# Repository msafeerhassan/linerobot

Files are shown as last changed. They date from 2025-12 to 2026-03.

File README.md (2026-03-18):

# Line Following Robot with PID
## Project Overview

Line Following Robot with PID project uses IR Sensors, Microcontroller and Motors to follow a line path on the floor. PID is a type of error-reduction algorithm implemented in such robots to reduce their errors and improve accuracy and precision.
## Project Details
This project is built under Hack Club's Blueprint Program. Custom shape PCB is be used as chassis for the car. PCB covers all components routing alongwith components mounting and soldering. This reduces the wires and improve the project's appearance. Moreover, it reduces the weight due to separate chassis making it more efficient.
N20 Gear Motors with encoders and DRV8833 Motor Driver alongwith QTR 8 Channel IR Sensor Array and ESP32 S3 Devkit are being used. Several capacitors are added to improve the current flow. A Lithium Battery powers this whole project. ESP32 is powered by 5V which is regulated via a Buck Convertor. Motors are powered by 6V and this too is regulated through a 6V 5A Buck Converter.

### PCB:





### Schematic Diagram:



### 3D Model Images:





### Why I made this project?

This was my first ever Hardware Project involving Schematic Design and PCB. I chose this project to strengthen my knowledge and skills of using sensors, microcontrollers etc. I learnt a lot about capacitance, optimum current flow and how sensors work inside. This robot will be used to compete in Line Following Robot competitions like: https://www.dmtsnust.com/nerc/. This project, though difficult but still made me believe that I can build efficient and great Hardware Projects too.

### How it will work
Firstly, battery powers everything and voltage is regulated via Buck Convertors. 
Then the IR Sensor Array gives readings to the ESP32 and based on that, ESP32 alters the speed of motors via Motor Driver.
This allows Robot to stay on line.
When PID is implemented, after this step the ESP32 counts error Value and based on that some manual variables are adjusted that results in increased accuracy and precision.
This loop continues until the robot reaches end of line and then it will stop.

### How to use it?

Firstly, order the PCB from PCB Manufacturing Service. I used JLCPCB: http://jlcpcb.com/ because they offer great and high quality services.
Then order all the components listed in the Bill of Materials.
Solder them all onto the PCB and fully assemble it.
Flash the firmware inside the ESP32. Make sure to adjust variables for better results.
BOOM!!! YOU MADE A COOL LINE FOLLOWING ROBOT.

## Bill of Materials (BOM)

| Item Name | Quantity | Link | Cost |
|:---|---:|:---|:---|
| ESP32-DevKit-S3-WROOM1 | 1 | [Link](https://epro.pk/product/pre-soldered-esp32-s3-wroom-1-development-board-2-4g-wifi-bt-module/) | $6.41  |
| DRV8833 Motor Driver | 1 | [Link](https://epro.pk/product/tb6612-drv8833-dual-motor-driver-module-1a-h-bridge-for-arduino-robotics/) | $1.98  |
| 6V N20 Gear Motor with encoder, wheel and mounting brackets | 2 | [Link](https://www.aliexpress.com/item/1005004110888400.html) | $16.35 |
| 5A Buck DC-DC Converter 7.4V to 6V | 1 | [Link](https://www.aliexpress.com/item/4000496873234.html) | $4.84  |
| 7.4V to 5V 1A DC-DC Fixed Buck Convertor (for ESP32) | 1 | [Link](https://www.aliexpress.com/item/1005006005553178.html) | $1.86  |
| 470 µF, 16 V aluminium electrolytic capacitor | 2 | [Link](https://epro.pk/product/470uf-16v-aluminum-electrolytic-capacitor/) | $0.11  |
| 220 µF, 10 V aluminium electrolytic capacitor | 1 | We'll buy it ourself | $0.00  |
| 100 nF Ceramic Capacitor | 2 | [Link](https://epro.pk/product/0-1uf-100nf-100000pf-104-ceramic-capacitor-in-pakistan/) | $0.02  |
| 8 Channel IR Sensor Array | 1 | [Link](https://epro.pk/product/qtr-8rc-line-following-reflectance-ir-sensor-8-channel-line-following-line-tracking-array-module/) | $2.30  |
| LiPo Battery 7.4V 1500mAH | 1 | [Link](https://epro.pk/product/zop-power-7-4v-1500mah-li-po-rechargeable-battery-pack/) | $10.04 |
| PCB | 1 | No Link:( | $36.25 |
| Push Switch Button | 1 | [Link](https://epro.pk/product/slider-on-off-switch/) | $0.05  |
| TAXES:( | 0 | No Link:( | $16.14 |
| Total Cost | 0 | | $96.35 |

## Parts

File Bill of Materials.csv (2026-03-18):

Item Name | Quantity | Sourcing Link | Cost
ESP32-DevKit-S3-WROOM1 | 1 | https://epro.pk/product/pre-soldered-esp32-s3-wroom-1-development-board-2-4g-wifi-bt-module/ | $6.41
DRV8833 Motor Driver | 1 | https://epro.pk/product/tb6612-drv8833-dual-motor-driver-module-1a-h-bridge-for-arduino-robotics/ | $1.98
6V N20 Gear Motor with encoder, wheel and mounting brackets | 2 | https://www.aliexpress.com/item/1005004110888400.html | $16.35
5A Buck DC-DC Converter 7.4V to 6V | 1 | https://www.aliexpress.com/item/4000496873234.html | $4.84
7.4V to 5V 1A DC-DC Fixed Buck Convertor (for ESP32) | 1 | https://www.aliexpress.com/item/1005006005553178.html | $1.86
470 µF, 16 V aluminium electrolytic capacitor | 2 | https://epro.pk/product/470uf-16v-aluminum-electrolytic-capacitor/ | $0.11
220 µF, 10 V aluminium electrolytic capacitor | 1 | We'll buy it ourself | $0.00
100 nF Ceramic Capacitor | 2 | https://epro.pk/product/0-1uf-100nf-100000pf-104-ceramic-capacitor-in-pakistan/ | $0.02
8 Channel IR Sensor Array | 1 | https://epro.pk/product/qtr-8rc-line-following-reflectance-ir-sensor-8-channel-line-following-line-tracking-array-module/ | $2.30
LiPo Battery 7.4V 1500mAH | 1 | https://epro.pk/product/zop-power-7-4v-1500mah-li-po-rechargeable-battery-pack/ | $10.04
PCB | 1 | No Link:( | $36.25
Push Switch Button | 1 | https://epro.pk/product/slider-on-off-switch/ | $0.05
TAXES:( |  | No Link:( | $16.14
Total Cost |  |  | $96.35

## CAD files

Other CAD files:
CAD/Main Design.step
CAD/Main Design.f3z

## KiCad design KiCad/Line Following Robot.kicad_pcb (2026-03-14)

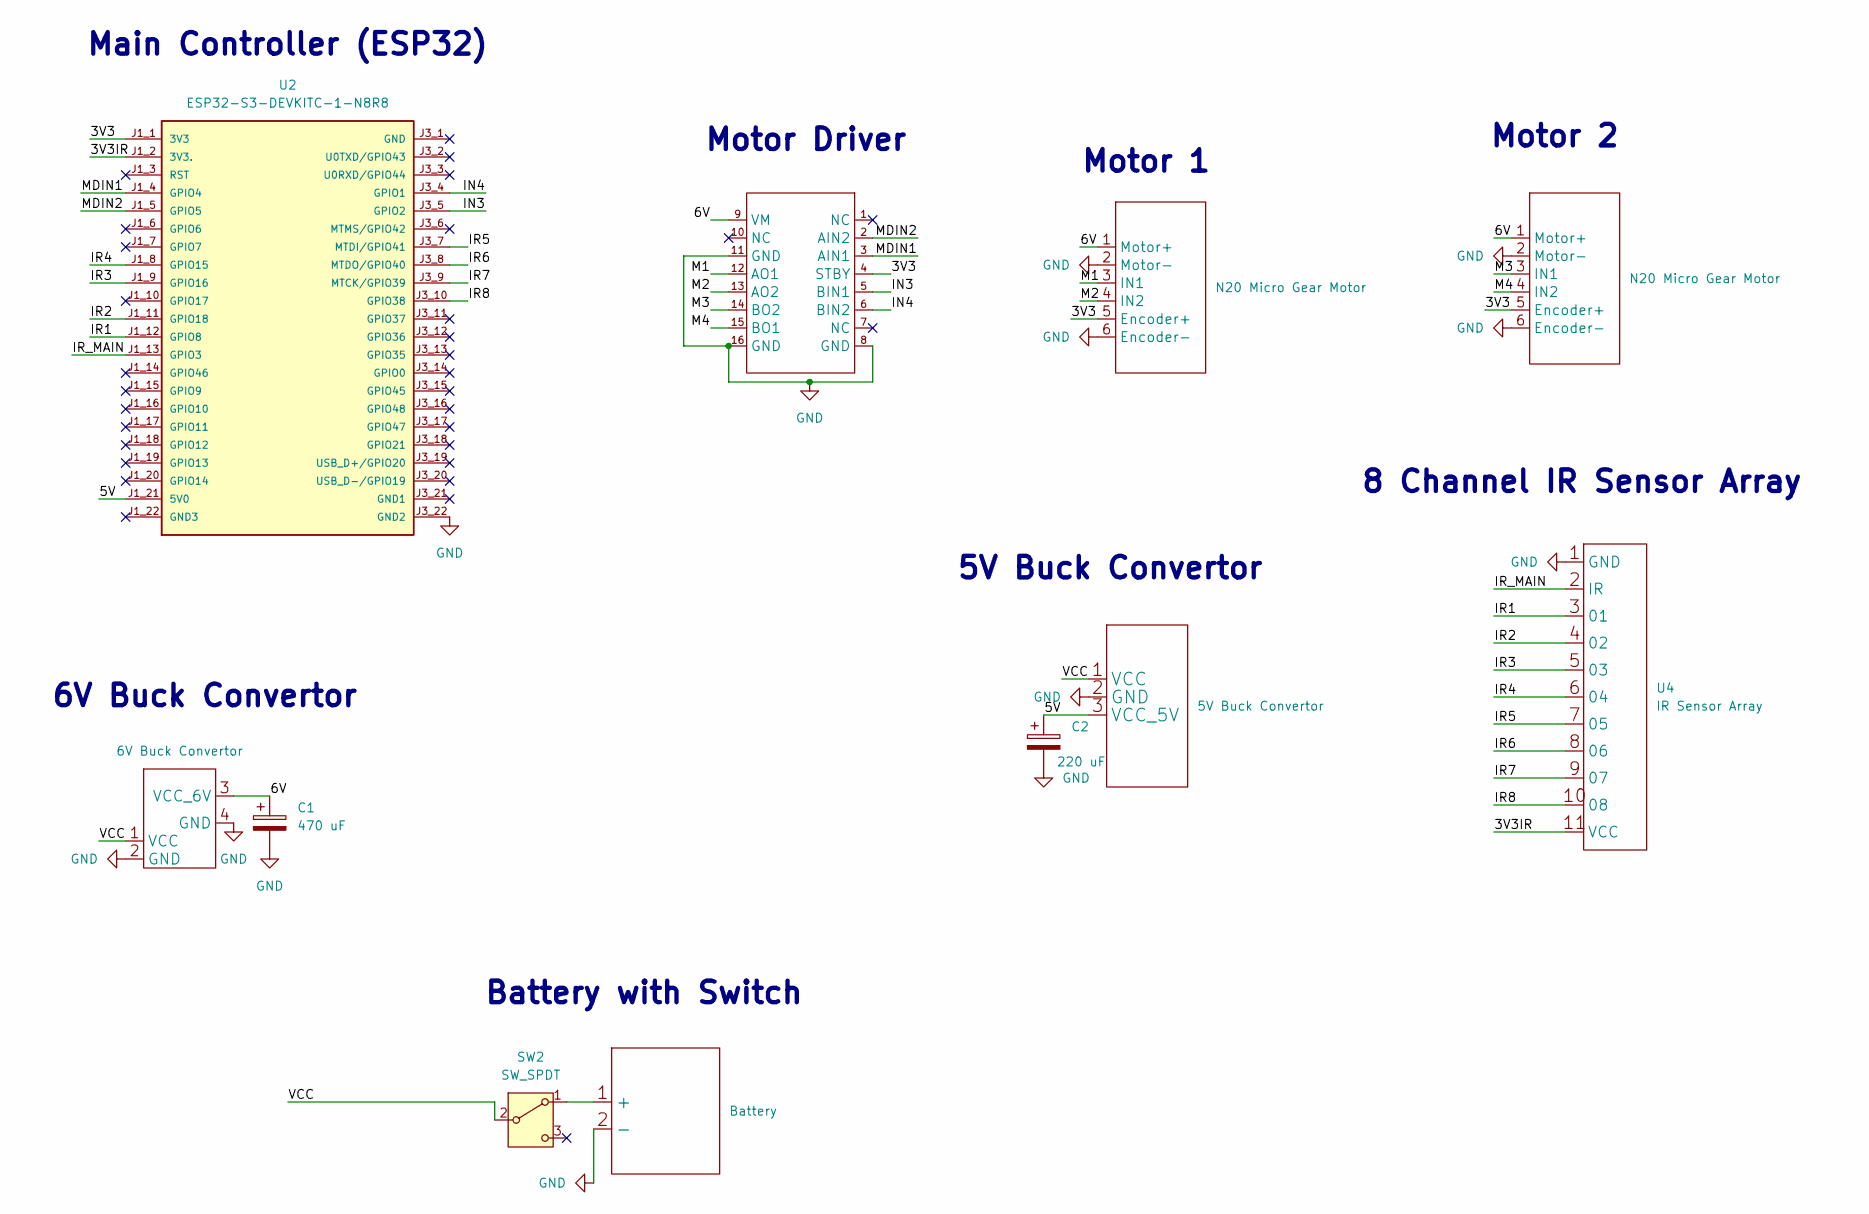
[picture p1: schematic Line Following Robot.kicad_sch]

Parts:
A1, A2: N20 Micro Gear Motor; Motor
C1: 470 uF; Capacitor
C2: 220 uF; Capacitor
SW2: SW_SPDT; SW_Slide-03_Wuerth-WS-SLTV_10x2.5x6.4_P2.54mm
U1: 5V Buck Convertor
U2: ESP32-S3-DEVKITC-1-N8R8
U3: 6V Buck Convertor; 6V New Buck Convertor
U4: IR Sensor Array
U6: PinHeader_1x08_P2.54mm_Vertical
U7: Battery

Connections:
/3V3: A1.5 (Encoder+), A2.5 (Encoder+), U2.J1_1 (3V3), U6.4 (STBY)
/3V3IR: U2.J1_2 (3V3.), U4.11 (VCC)
/5V: C2.1, U1.3 (VCC_5V), U2.J1_21 (5V0)
/6V: A1.1 (Motor+), A2.1 (Motor+), C1.1, U3.3 (VCC_6V), U6.9 (VM)
/IN3: U2.J3_5 (GPIO2), U6.5 (BIN1)
/IN4: U2.J3_4 (GPIO1), U6.6 (BIN2)
/IR1: U2.J1_12 (GPIO8), U4.3 (01)
/IR2: U2.J1_11 (GPIO18), U4.4 (02)
/IR3: U2.J1_9 (GPIO16), U4.5 (03)
/IR4: U2.J1_8 (GPIO15), U4.6 (04)
/IR5: U2.J3_7 (MTDI/GPIO41), U4.7 (05)
/IR6: U2.J3_8 (MTDO/GPIO40), U4.8 (06)
/IR7: U2.J3_9 (MTCK/GPIO39), U4.9 (07)
/IR8: U2.J3_10 (GPIO38), U4.10 (08)
/IR_MAIN: U2.J1_13 (GPIO3), U4.2 (IR)
/M1: A2.3 (IN1), U6.12 (AO1)
/M2: A2.4 (IN2), U6.13 (AO2)
/M3: A1.3 (IN1), U6.14 (BO2)
/M4: A1.4 (IN2), U6.15 (BO1)
/MDIN1: U2.J1_4 (GPIO4), U6.3 (AIN1)
/MDIN2: U2.J1_5 (GPIO5), U6.2 (AIN2)
/VCC: SW2.2 (B), U1.1 (VCC), U3.1 (VCC)
GND: A1.2 (Motor-), A1.6 (Encoder-), A2.2 (Motor-), A2.6 (Encoder-), C1.2, C2.2, U1.2 (GND), U2.J3_22 (GND2), U3.2 (GND), U3.4 (GND), U4.1 (GND), U6.8 (GND), U6.11 (GND), U6.16 (GND), U7.2 (-)
unnamed: SW2.1 (A), U7.1 (+)

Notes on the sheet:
6V Buck Convertor
Motor Driver
Motor 2
5V Buck Convertor
8 Channel IR Sensor Array
Main Controller (ESP32)
Battery with Switch
Motor 1

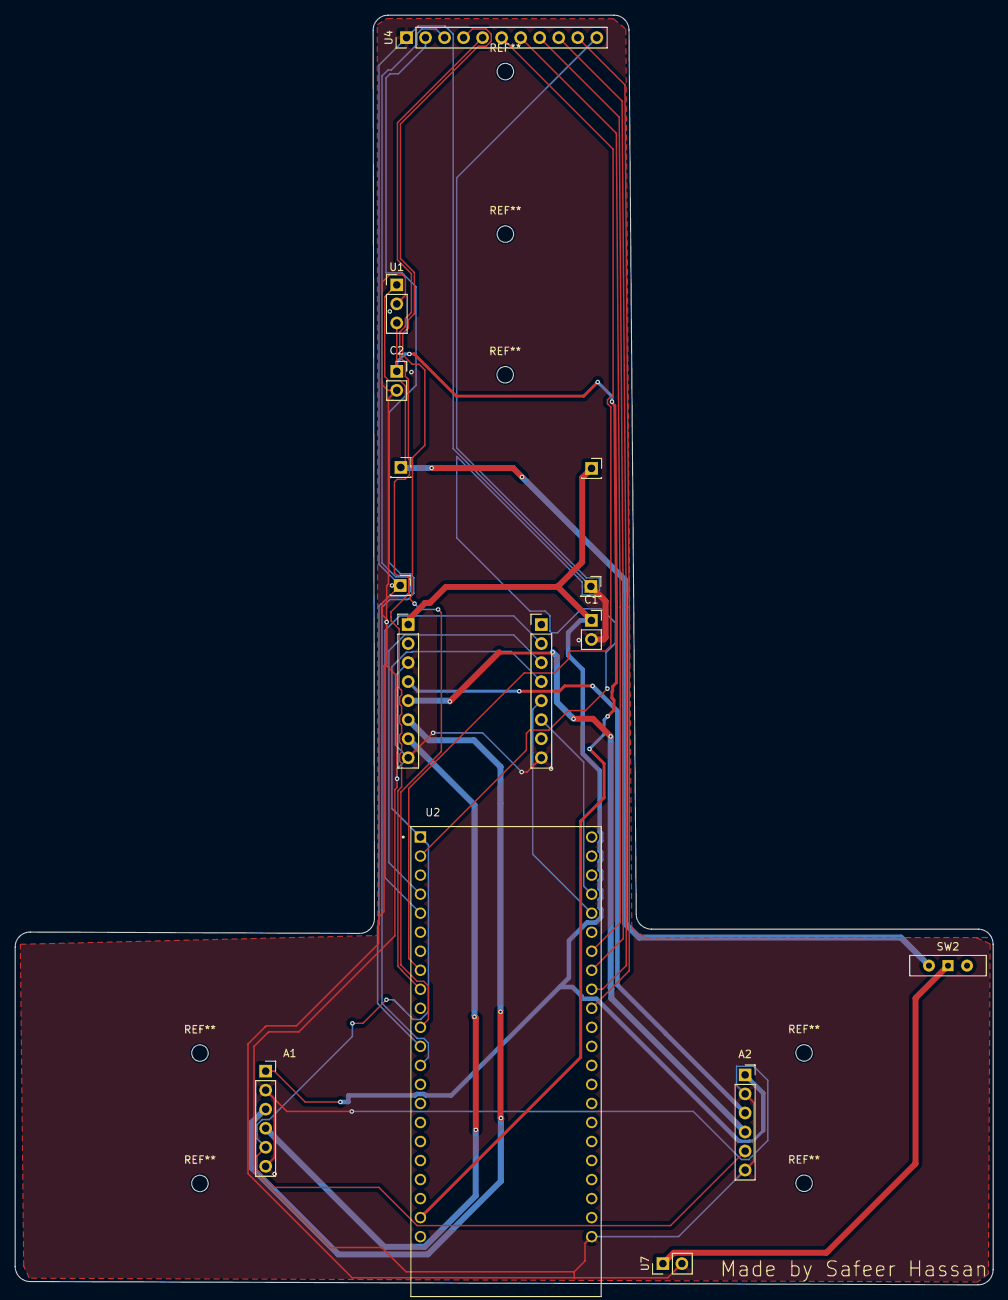
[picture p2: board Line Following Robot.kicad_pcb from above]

Board: 2 copper layers, 130.5 x 169.5 mm, 11 parts (0 on the bottom side), 24 nets.

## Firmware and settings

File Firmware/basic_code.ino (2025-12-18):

const int ir1 = 14;
const int ir2 = 7;
const int ir3 = 6;
const int ir4 = 1;
const int ir5 = 0;
const int ir6 = 21;
const int ir7 = 20;
const int ir8 = 19;
const PWMA = 2;
const PWMB = 3;
const AIN1 = 22;
const BIN1 = 23;
const AIN2 = 5;
const BIN2 = 6;
const int frequencyPWM = 1000;
const int resolution = 8;
int speed = 150;

void setup()
{
  Serial.begin(115200);
  pinMode(ir1, INPUT);
  pinMode(ir1, INPUT);
  pinMode(ir1, INPUT);
  pinMode(ir1, INPUT);
  pinMode(ir1, INPUT);
  pinMode(ir1, INPUT);
  pinMode(ir1, INPUT);
  pinMode(ir1, INPUT);

  pinMode(AIN1, OUTPUT);
  pinMode(AIN2, OUTPUT);            
  pinMode(BIN1, OUTPUT);            
  pinMode(BIN2, OUTPUT);

  digitalWrite(AIN1, LOW);
  digitalWrite(AIN2, LOW);
  digitalWrite(BIN1, LOW);
  digitalWrite(BIN2, LOW);

  ledcAttach(PWMA, frequencyPWN, resolutionPWN);
  ledcAttach(PWMB, frequencyPWN, resolutionPWN);
  ledcWrite(PWMA, 0);
  ledcWrite(PWMB, 0);
  
  Serial.println("Ready!");
  delay(2000);
}

void loop() {
  int ir1 = digitalRead(ir1);
  int ir2 = digitalRead(ir2);
  int ir3 = digitalRead(ir3);
  int ir4 = digitalRead(ir4);
  int ir5 = digitalRead(ir5);
  int ir6 = digitalRead(ir6);
  int ir7 = digitalRead(ir7);
  int ir8 = digitalRead(ir8);

  Serial.print("Sensors Data: ")
  Serial.print(ir1);
  Serial.print(" ");
  Serial.print(ir2);
  Serial.print(" ");
  Serial.print(ir3);
  Serial.print(" ");
  Serial.print(ir4);
  Serial.print(" ");
  Serial.print(ir5);
  Serial.print(" ");
  Serial.print(ir6);
  Serial.print(" ");
  Serial.print(ir7);
  Serial.print(" ");
  Serial.print(ir8);
  Serial.print(" ");

  int leftTyreSpeed = speed;
  int rightTyreSpeed = speed;

  if(ir1 || ir2 || ir3) {
    leftTyreSpeed = speed/2;
    rightTyreSpeed = speed;
  }
  else if (ir6 || ir7 || ir8) {
    leftTyreSpeed = speed;
    rightTyreSpeed = speed/2;
  }
  else if (ir4||ir5) {
    leftTyreSpeed = speed;
    rightTyreSpeed = speed;
  }
  else {
    leftTyreSpeed = 0;
    rightTyreSpeed = 0;
  }

  setMotorSpeed(leftTyreSpeed, rightTyreSpeed);
  delay(50);
}

void setMotorSpeed(int leftTyreSpeed, int rightTyreSpeed) {
  if(leftTyreSpeed > 0)
  {
    digitalWrite(AIN1, HIGH);
    digitalWrite(AIN2, LOW);
  }
  else if (leftTyreSpeed < 0)
  {
    digitalWrite(AIN1, LOW);
    digitalWrite(AIN2, HIGH);
  }
  else
  {
    digitalWrite(AIN1, LOW);
    digitalWrite(AIN2, LOW);
  }
  
  ledcWrite(PWMA, abs(leftTyreSpeed));

  if(rightTyreSpeed > 0)
  {
    digitalWrite(BIN1, LOW);
    digitalWrite(BIN2, HIGH);
  }
  else if (rightTyreSpeed < 0)
  {
    digitalWrite(BIN1, HIGH);
    digitalWrite(BIN2, LOW);
  }
  else
  {
    digitalWrite(BIN1, LOW);
    digitalWrite(BIN2, LOW);
  }

  ledcWrite(PWMB, abs(rightTyreSpeed));
}

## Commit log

2025-12-04 kicad files upload
    [Line Following Robot.kicad_pcb, Line Following Robot.kicad_sch]
2025-12-04 uploaded BoM
    [Bill of Materials.xlsx]
2025-12-04 BoM in excel and csv format
    [Bill of Materials.csv, Bill of Materials.xlsx]
2025-12-17 changes committed
    [Line Following Robot.kicad_pcb, Line Following Robot.step]
2026-01-04 updated BoM with lower cost :)
    [BoM.csv]
2026-01-09 updated CAD Files
2026-01-09 updated KiCad files
    [Line Following Robot.kicad_pcb, Line Following Robot.kicad_sch]
2026-01-09 Revise README with updated project specifications
    Updated project details and specifications for the Line Following Robot. Changed ESP32 Devkit to ESP32 S3 and added PCB images.
2026-02-09 Enhance README with new images and project details
    Updated images and descriptions in the README for PCB, schematic diagrams, and 3D models.
2026-02-09 Whole Project Recommit - Fixed Schematic, PCB, Gerber, 3D Model
    [BoM.csv, Line Following Robot.kicad_pcb, Line Following Robot.kicad_sch]
2026-02-10 fixed pcb
    [Line Following Robot.kicad_pcb]
2026-02-14 added step file
    [BoM.csv, Line Following Robot.kicad_pcb, Line Following Robot.kicad_sch]
2026-02-15 Enhance README with project details and instructions
    Added sections for PCB, schematic diagrams, 3D model images, project motivation, usage instructions, and bill of materials.
2026-02-15 Removed everything bcz got messed up
    [BoM.csv, Line Following Robot.kicad_pcb, Main Design.f3z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]
2026-02-15 Add all files again....
    [Bill of Materials.csv, Line Following Robot.kicad_pcb, Line Following Robot.kicad_sch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]
2026-03-04 added f3z file
    [Main Design.f3z]
2026-03-07 fixed everything
    [Bill of Materials.csv, Line Following Robot.kicad_pcb, Line Following Robot.kicad_sch]
2026-03-08 fixed pcb and schematic
    [Line Following Robot.kicad_pcb, Line Following Robot.kicad_sch]
2026-03-14 fixed footprint
    [Line Following Robot.kicad_pcb]
2026-03-18 updated BoM
    [Bill of Materials.csv]
2026-03-18 updated BoM and readme
    [Bill of Materials.csv]
